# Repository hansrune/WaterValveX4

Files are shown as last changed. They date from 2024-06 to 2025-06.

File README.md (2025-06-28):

# Valve Controller X4

Work in progress / still a prototype...

A DYI 4x valve controller based on ESP32c3. This device is mainly intended for irrigation control, typically using 12V solenoid valves. You can also use ball valves with automatic return on power off.

This board is tested with ESPhome and ESPEasy [firmware](#firmwares) (build instructions below), and is easily used with home automation systems that support MQTT auto discovery, the native Home Assistant API, and the many [controllers that ESPEasy supports](https://espeasy.readthedocs.io/en/latest/Controller/_Controller.html)

## Introduction

Some of the main features and benefits

- **4x outputs**
    - For controlling up to four valves at a time
    - Each valve should draw less than 1A - or you can add to the PCB trace thickness using wire
- **Flow sensor input**
    - A flow sensor input is available
    - Can be open collector / hall sensor. Pulled up to 3.3V level internally. 5V supply on terminal
- **I2C support**
    - An I2C pin header with power supply is available to use with I2C sensors
    - ... or you can use the same GPIO pins for any other purpose of your choise
- **WiFi based**
    - This is almost a must have for most home automation systems
    - OTA support
    - Configuration backup, restore and bulk updates.
- **Firmware of your choise**
    - ESPEasy with Domoticz over http. Device creation uses virtual sensors
    - ESPEasy with Domotics and Home Assistant via MQTT. Device creation uses a MQTT configuration text file.
    - ESPHome to Home Assistant via MQTT and auto discovery
    - ESPHome to Domoticz via MQTT and auto discovery
    - ... and as the hardware supports using both Arduino and ESP-IF development kits, almost any other firmware can be created.
- **Seed Studio XIAO ESP32C3**
    - This device is shielded and comes with an external IPX antenna connector
    - FCC and CE regulations approved

## Setup and mounting

The main parts includes a simple flow sensor and a pressure reduction device:

<p align="center">
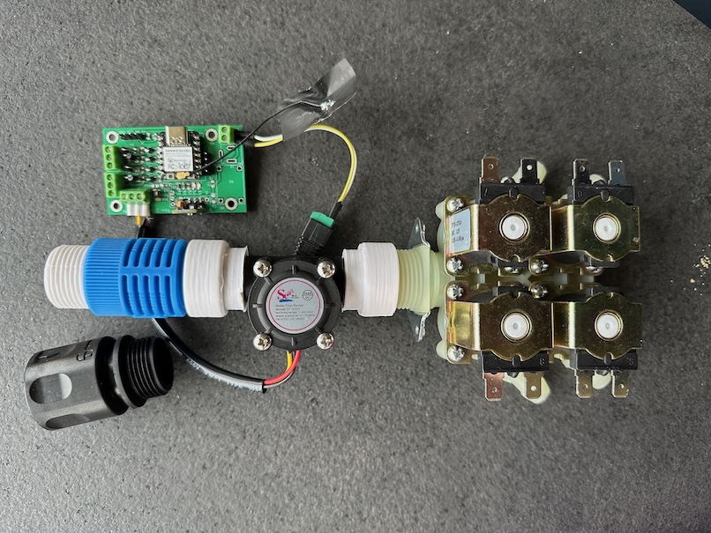
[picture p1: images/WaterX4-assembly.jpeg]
    
</p>

The adapter parts are [3D prints](./FreeCAD/README.md)

I use a long box with a closing / latched lid. This is designed for outdoor use. Will tolerate rain, but not frost.

<p align="center">
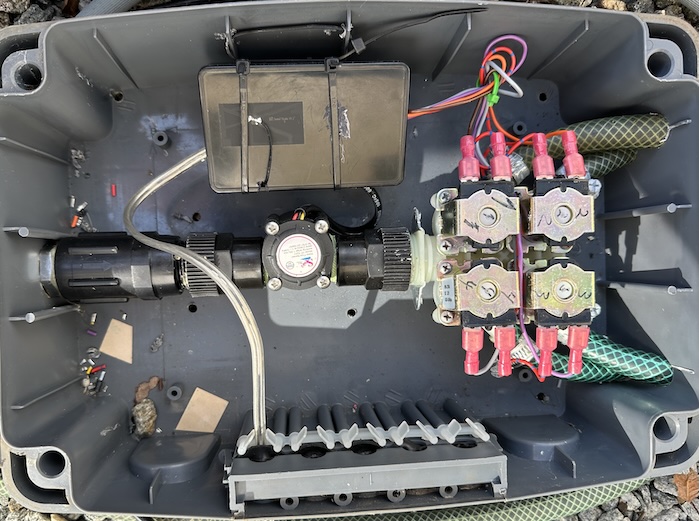
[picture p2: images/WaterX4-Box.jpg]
    
</p>

Please note the bottom holes. In case water is leaked, it has a way to drain out of the box

## Indicators

Each of the four valve outputs has a LED indicator at the back of the PCB

- LED D11 will indicate low level input from the flow meter
- LED D1
  - no change indicates out of power, device death/freeze or other
  - a duty cycle 1:1 will indicate a reset is ongoing
<!--
  - will blink with a duty cycle 1-4 or 4-1 to indicate valve closed or open
-->

## Implementation and design

The schematic diagram is [available here](KiCad/WaterValveX4-schema-2.0.1.pdf). The [KiCad EDA](https://www.kicad.org/) project is in the [same folder](./KiCad)

### GPIO pin usage

| PIN | Capabilty | Function |
|---|---|---|
| GPIO2 | Acticve low output | LED D2 - not used |
| GPIO3 | Active high output | Valve 1 |
| GPIO4 | Active high output | Valve 2 |
| GPIO5 | Active high output | Valve 3 |
| GPIO6 | I2C | SDA |
| GPIO7 | I2C | SCL |
| GPIO8 | Active high output | Valve 4 |
| GPIO9 | Active low out | Status LED |
| GPIO10 | Pulled up input | Flow meter input |
| GPIO20 | RX / 1-wire | Serial or 1-wire sensor |
| GPIO21 | TX / 1-wire | Serial or 1-wire sensor |

## Hardware - getting started

This project uses my [KiCad-lib-ESP32 repository](https://github.com/hansrune/KiCad-lib-ESP32.git) as a [git submodule](https://www.git-scm.com/book/en/v2/Git-Tools-Submodules). To check this out, use the following:

```bash
git clone --recurse-submodules https://github.com/hansrune/WaterValveX4.git 
```

### Materials used

This project uses the [Seed Studio XIAO ESP32C3 RISC-V module](https://www.seeedstudio.com/Seeed-XIAO-ESP32C3-p-5431.html). This tiny device has proven to be more reliable than most ESP8266 modules used in earlier versions. This module also comes with an IPX connector for connecting an external antenna, and is delivered with a simple external antenna for good range. This device is also EMI shielded and certified.

<!--
A ball valve like [these HSH-FLO valves](https://www.ebay.com/itm/121728665101?var=420727385309) uses metal gears, and also have a manual override possibility. Despite the moderate cost, I have found them very reliable. Manufacturer claims 100k operations. I typically use a 2 or some times 3-port version, size 3/4" DN20, DC12/24V and with CR05-01 wiring, including a manual overrride whell option.
-->
A 4x valve like the below attached with a washing machine attachment hose

<p align="center">
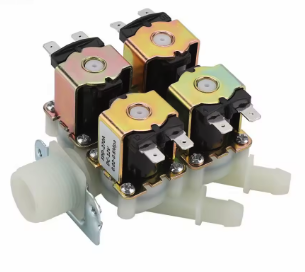
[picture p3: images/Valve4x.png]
    
</p>

A selection of 3D printable (STL and FreeCAD) adapters is available [here](./FreeCAD/README.md)

Any available 12V DC power supply delivering 2A or more should do for the control board and the valves.

There are many options and possible pinouts for DC-DC converters for the 12V to 5V conversion. A linear regulator (L7805) will need a heatsink, so a DC-DC converter is recommended.

<p align="center">
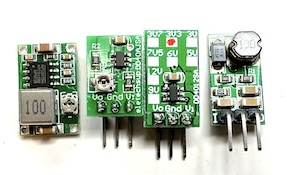
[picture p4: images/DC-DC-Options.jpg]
    
</p>

The MOSFETs need a low Vgs trigger voltage, i.e. well under 3V on full load. I have used Si2302/N025P for the N-channel, SOT-23 package.

Resistors are 0805 size. Screw terminals are 3.5mm, which is a tight fit when ferrules are being used.

For more information, use [this KiCad BOM](KiCad/WaterValveX4-BOM.csv)

## Hardware assembly

Soldering a prototype by hand is possible if you have a steady hand and a small solder iron tip. A microscope is recommended to inspect the solder joints properly.

Recommend to do the SMD parts first, then other components. 

### Hardware tests

You should test at least the following **before adding the ESP32 module**:

- Attach a battery and check that the valve can be operated both NO and NC
- Add power and check that 5V conversion is OK
- Apply 5V to GPIO 1, 5, 3 and 8 in turn to check that the output works with the indicators at the PCB back side

## Firmwares

### ESPHome

ESPHome firmware can be set up from [this ESPHome configuration repository](https://github.com/hansrune/esphome-config) using the `test_waterx4.yaml` file as a template

Follow the [README](https://github.com/hansrune/esphome-config) for instructions on what you will likely want to change.

By default, MQTT auto discovery is being used. This should work out of the box with Home Assistant, Domoticz and other that support [Home Assistant MQTT Auto Discovery](https://www.home-assistant.io/integrations/mqtt/#mqtt-discovery)

In Home Assistant, the device has these controls. Valves are labelled a, b, c and d. The -1 is the controller instance

<p align="center">
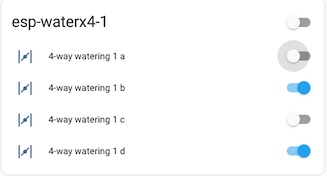
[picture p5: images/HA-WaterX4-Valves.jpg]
    
</p>

... and flow sensor / total counter:

<p align="center">
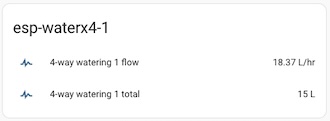
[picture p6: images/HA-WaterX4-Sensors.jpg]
    
</p>

### ESPEasy

ESPEasy can be used with a number of different controllers / home automation systms. A custom firmware build description is [available here](https://github.com/hansrune/ESPEasy-custom/blob/builds/custom/mega-20240822-1/README-custombuilds.md)

ESPEasy requires many settings. For configuration settings and rule files, you can upload the files from [this page](./ESPEasy/) as a starting point. Please make sure to change name, unit number, controller IP addresses, NTP, syslog host and latitude/longitude. This configuration uses both a MQTT controller and a Domoticz controller. Change to what you need.

## Bugs and tweaks

Version 2.0 of the PCB needs the flow sensor input components mounted as shown:

<p align="center">
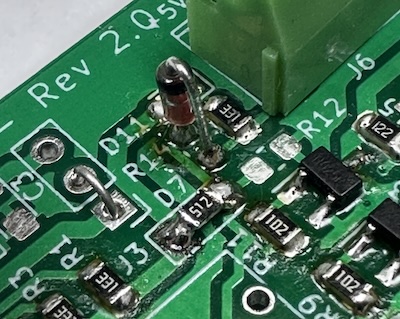
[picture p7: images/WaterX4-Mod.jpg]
    
</p>

- A 1N4148 diode replaces R14 - cathode faces terminal connector
- A 5.1 kohm resistor replaces D7 - for a pull-up
- R12 is not mounted

<!-- 

## How to contribute

-->

## Licensing

This project is licensed under the [GNU General Public License v3.0](GNU-LICENSE-V3.txt) for the software, [CERN-OHL-W](OHL-LICENSE.txt) for the hardware, and [CC BY-SA](CC-BY-SA-LICENCE.txt) for the documentation and ideas.

<p align="center" width="100%">
    
</p>

<!-- 
| **Open Source Licenses** | |
| ---|---|
| Hardware | [CERN-OHL-W](OHL-LICENSE.txt) |
| Software | [GNU General Public License v3.0](GNU-LICENSE-V3.txt) |
| Documentation / idea | [CC BY-SA](CC-BY-SA-LICENCE.txt) |
-->

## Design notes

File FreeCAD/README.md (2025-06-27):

## Adapters

Below is a selection of 3D printed adapters I have used. These are all BSP threads.

Printed with ABS filament and a 0.8mm nozzle for durability

- 1/2" female to 1/2" female

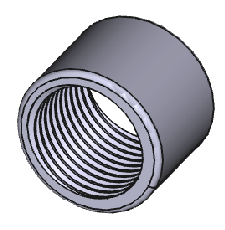
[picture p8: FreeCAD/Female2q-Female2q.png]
    

- 1/2" female to 3/4" female

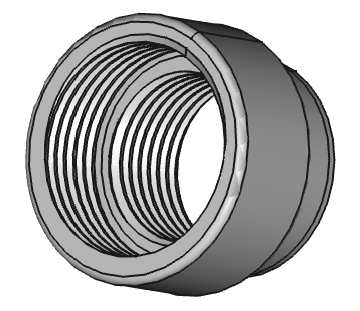
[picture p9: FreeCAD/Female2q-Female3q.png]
    

- 1/2" female to 3/4" male

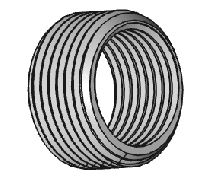
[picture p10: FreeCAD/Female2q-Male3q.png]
    

- 1/2" male to 1/2" male

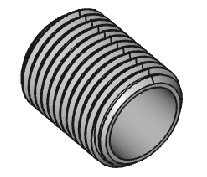
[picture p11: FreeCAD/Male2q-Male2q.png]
    

- 3/4" male to 3/4" male

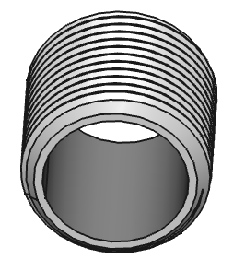
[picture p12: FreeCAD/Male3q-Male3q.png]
    

- 3/4" female to 3/4" female

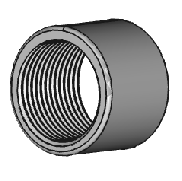
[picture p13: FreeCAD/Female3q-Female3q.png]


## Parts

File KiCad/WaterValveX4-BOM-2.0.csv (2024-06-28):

Id | Designator | Footprint | Quantity | Designation | Supplier and ref
1 | C3,C1 | CP_EIA-3216-18_Kemet-A_Pad1.58x1.35mm_HandSolder | 2 | 10uF
2 | J1,J5 | PinHeader_1x04_P2.54mm_Vertical | 2 | Conn_01x04_Male
3 | J2 | BarrelJack1 | 1 | Barrel_Jack
4 | J3 | PinHeader_1x03_P2.54mm_Vertical | 1 | Conn_01x03_Male
5 | Q1,Q2,Q3,Q4 | SOT-23_Handsoldering | 4 | IRLB3034
6 | R8,R6,R11,R9 | R_0805_2012Metric_Pad1.20x1.40mm_HandSolder | 4 | 1k
7 | R5,R4,R2 | R_0805_2012Metric_Pad1.20x1.40mm_HandSolder | 3 | 10k
8 | R7,R10,R3,R13,R15,R1,R16 | R_0805_2012Metric_Pad1.20x1.40mm_HandSolder | 7 | 330
9 | U2 | XIAO_ESP32C3_THT | 1 | SeedStudio XIAO ESP32 C3 v1
10 | U3 | TO-220-3_Vertical | 1 | L7805
11 | C2 | C_0805_2012Metric_Pad1.18x1.45mm_HandSolder | 1 | 100nF
12 | D2,D1,D11,D3,D8,D10,D5 | LED_0805_2012Metric_Pad1.15x1.40mm_HandSolder | 7 | LED
13 | J7,J8,J6 | TerminalBlock_Phoenix_PT-1,5-3-3.5-H_1x03_P3.50mm_Horizontal | 3 | Screw_Terminal_01x03
14 | U1 | DCDC_01 | 1 | Project_DCDC_01
15 | D4,D6,D9,D12 | D_DO-41_SOD81_P3.81mm_Vertical_KathodeUp | 4 | 1N4007
16 | J4 | PinHeader_1x01_P2.54mm_Vertical | 1 | Conn_01x01_Male
17 | H7,H5,H8,H6 | MountingHole_3.2mm_M3_ISO14580_Pad | 4 | MountingHole_Pad
18 | D7 | D_MiniMELF | 1 | 1N4148
19 | J9 | TerminalBlock_Phoenix_PT-1,5-2-3.5-H_1x02_P3.50mm_Horizontal | 1 | Screw_Terminal_01x02
20 | R14 | R_0805_2012Metric_Pad1.20x1.40mm_HandSolder | 1 | 2.2k
21 | R12 | R_0805_2012Metric_Pad1.20x1.40mm_HandSolder | 1 | 3.3k

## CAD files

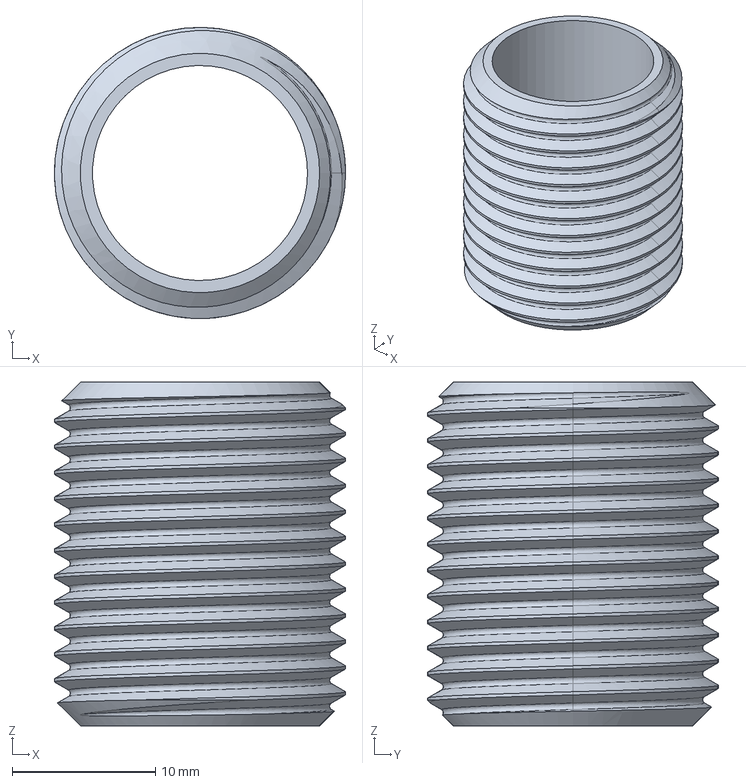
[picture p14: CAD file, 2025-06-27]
FreeCAD/Male2q-Male2q.FCStd
20.3 x 20.3 x 24.0 mm

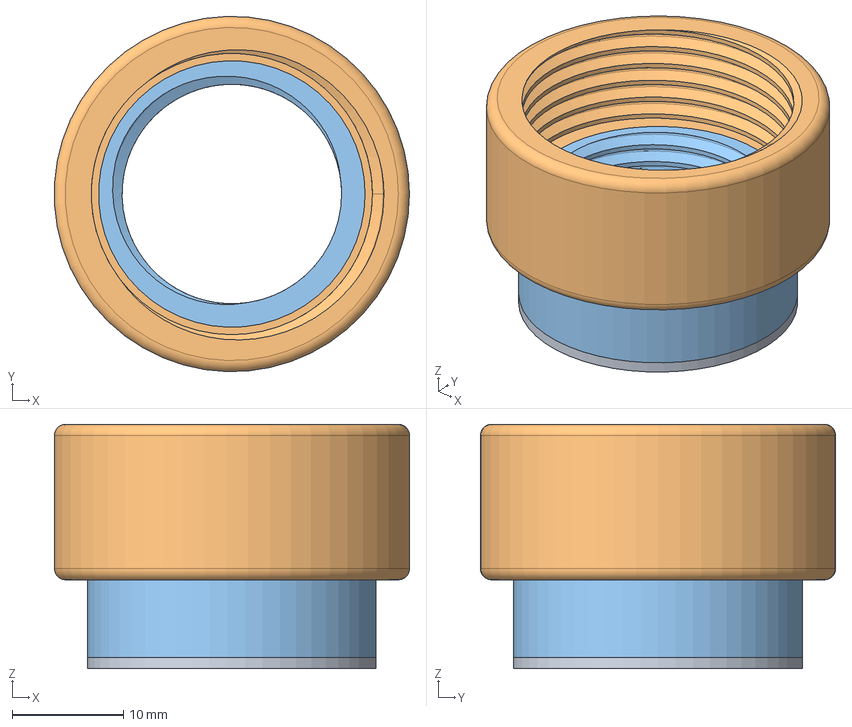
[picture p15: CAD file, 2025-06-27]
FreeCAD/Female2q-Female3q.FCStd
32.0 x 32.0 x 22.0 mm

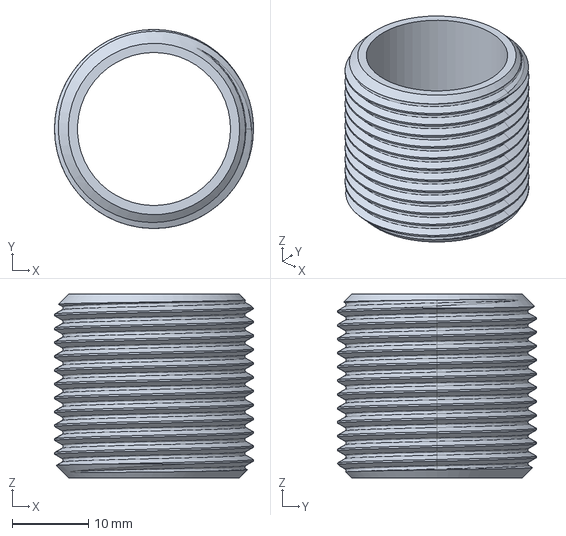
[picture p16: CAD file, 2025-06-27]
FreeCAD/Male3q-Male3q.FCStd
26.0 x 26.0 x 24.0 mm

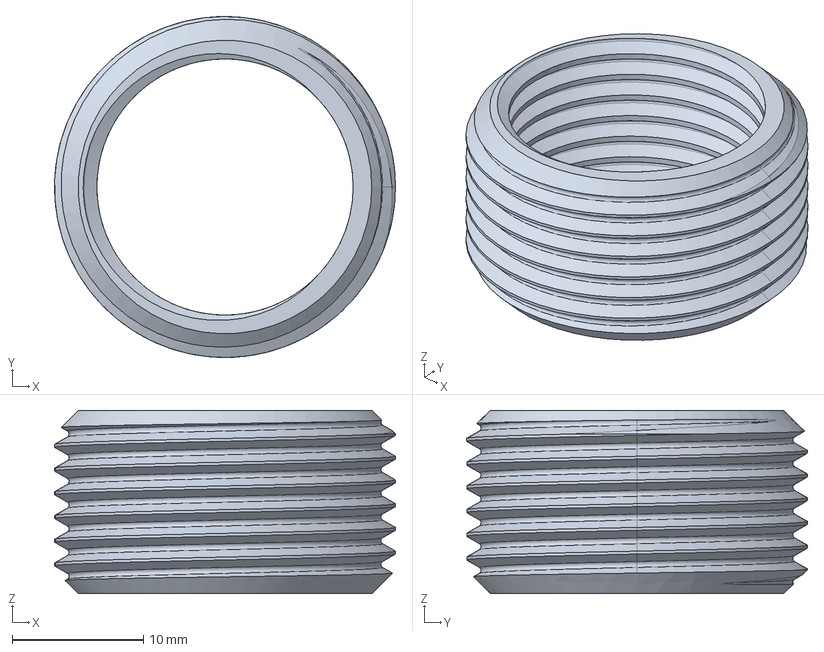
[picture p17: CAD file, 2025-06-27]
FreeCAD/Female2q-Male3q.FCStd
26.0 x 26.0 x 14.0 mm

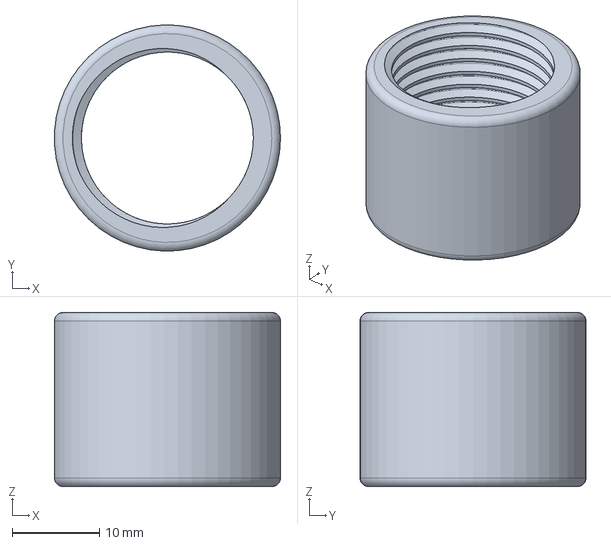
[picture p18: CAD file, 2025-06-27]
FreeCAD/Female2q-Female2q.FCStd
26.0 x 26.0 x 20.0 mm

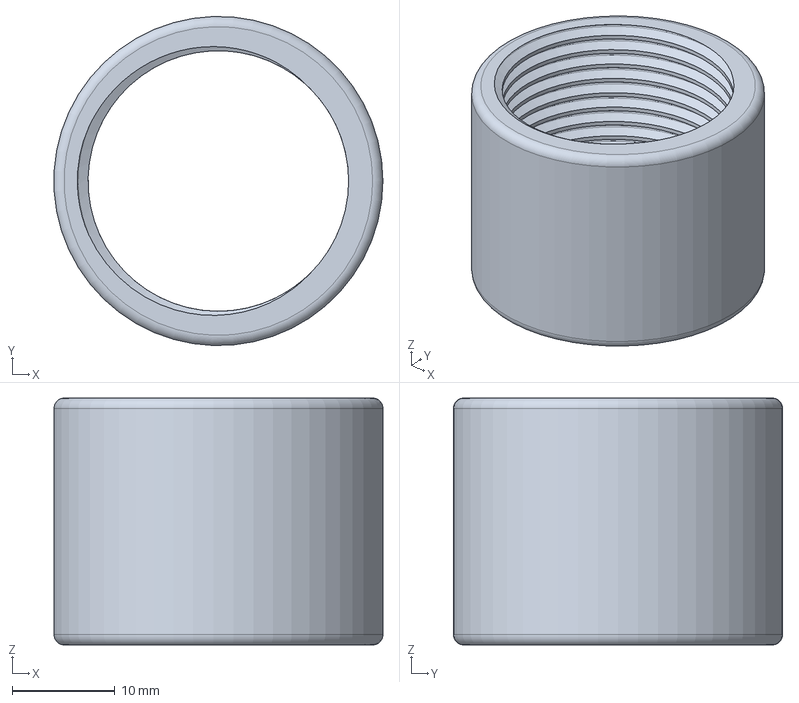
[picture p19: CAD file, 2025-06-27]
FreeCAD/Female3q-Female3q.FCStd
32.0 x 32.0 x 24.0 mm

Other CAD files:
FreeCAD/Male2q-Male2q.stl

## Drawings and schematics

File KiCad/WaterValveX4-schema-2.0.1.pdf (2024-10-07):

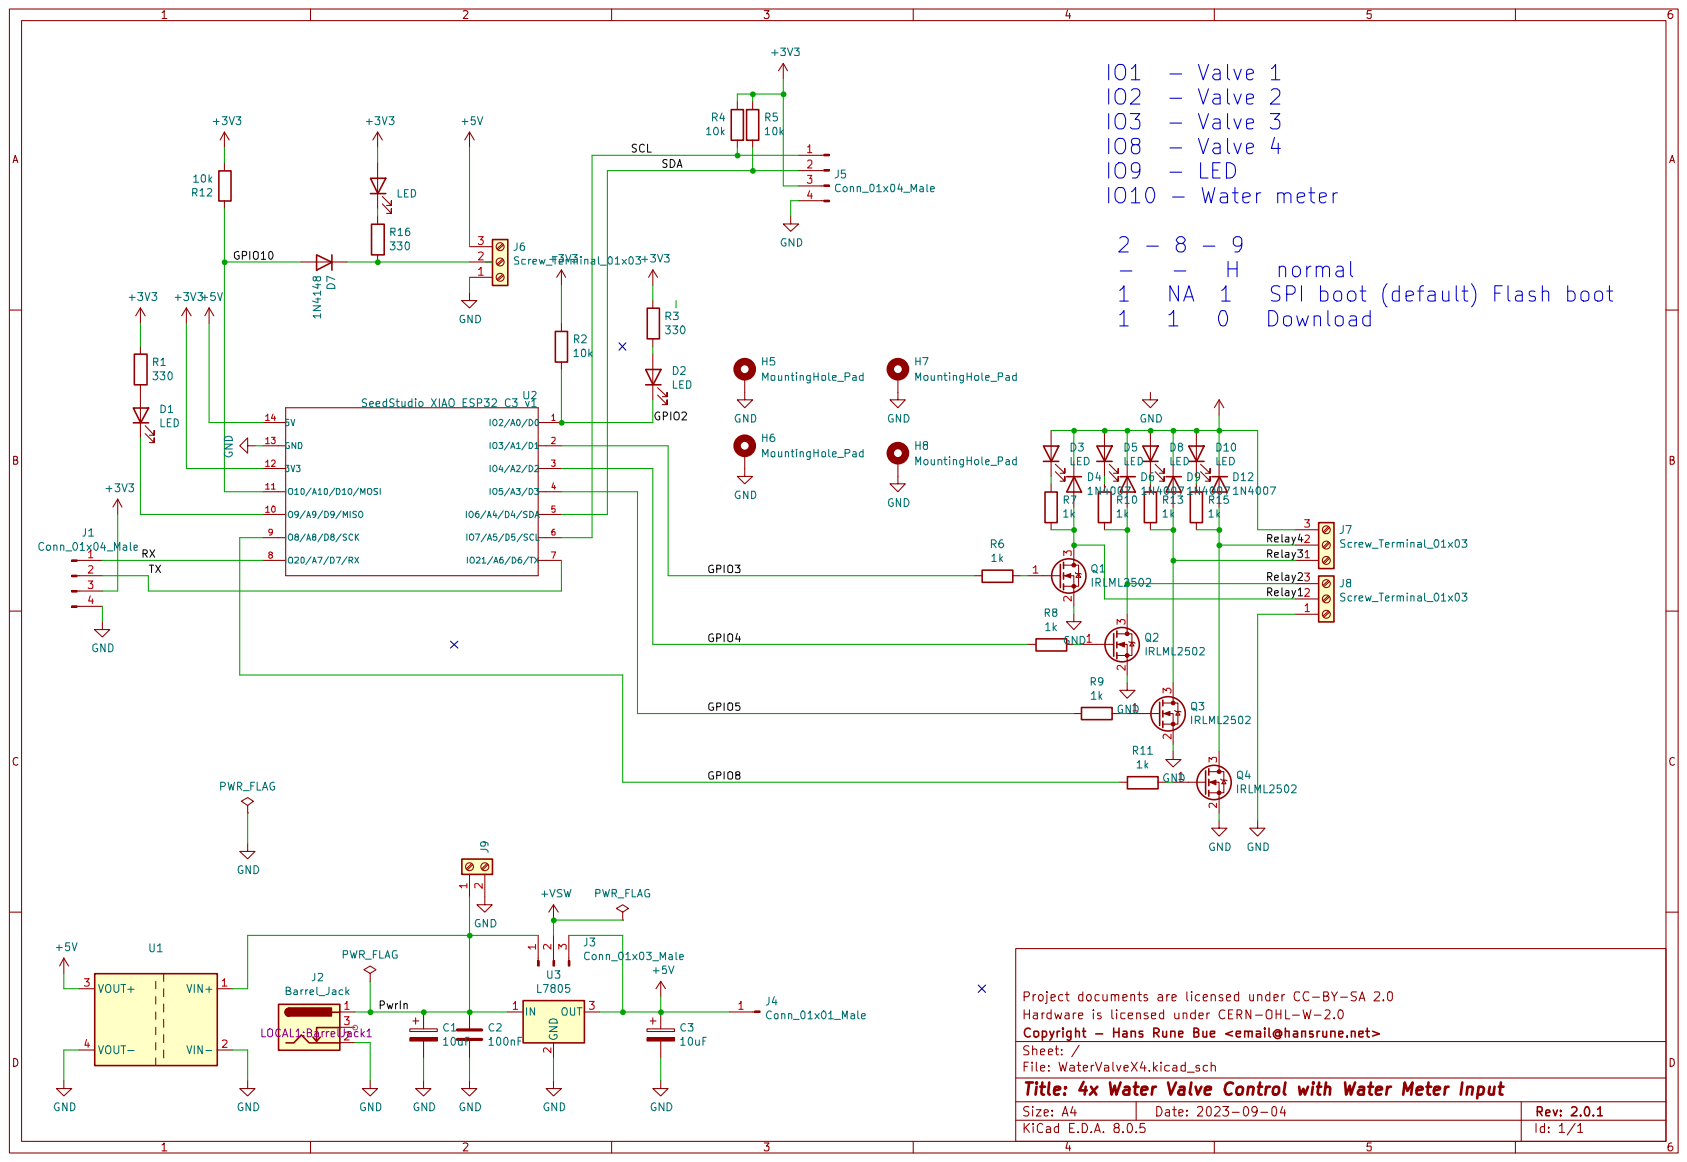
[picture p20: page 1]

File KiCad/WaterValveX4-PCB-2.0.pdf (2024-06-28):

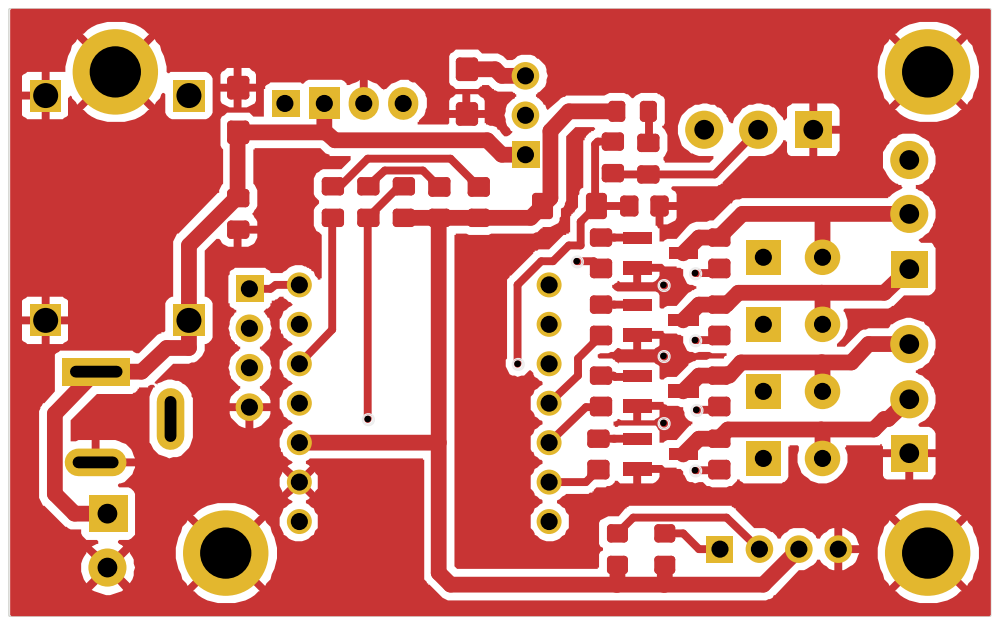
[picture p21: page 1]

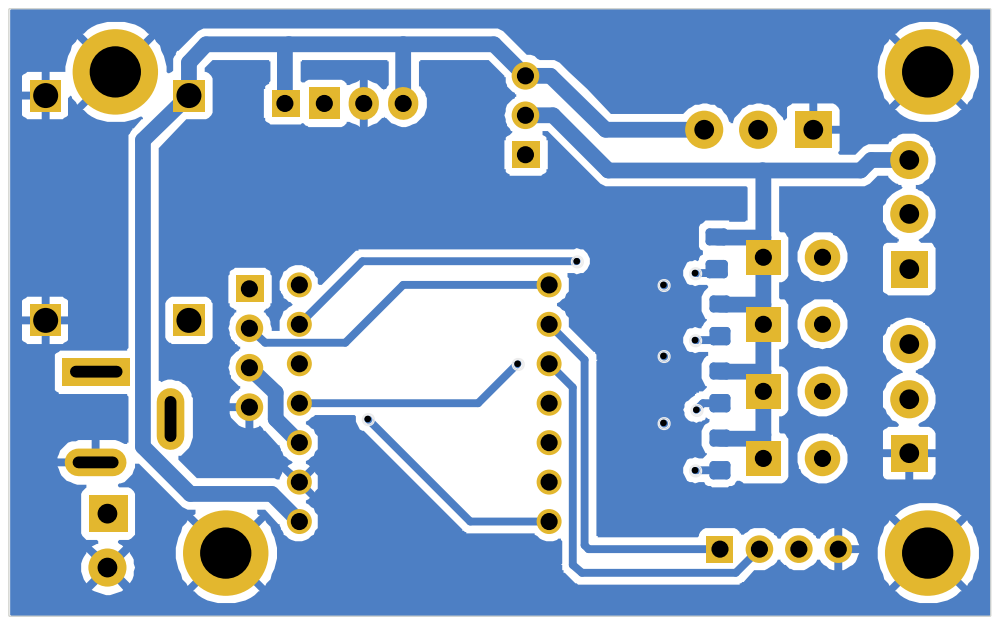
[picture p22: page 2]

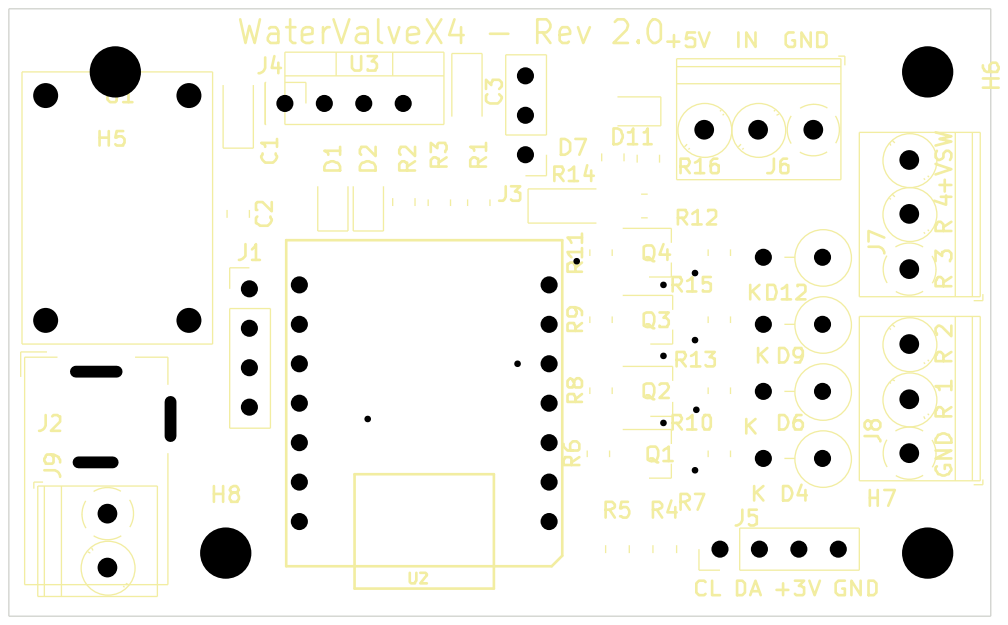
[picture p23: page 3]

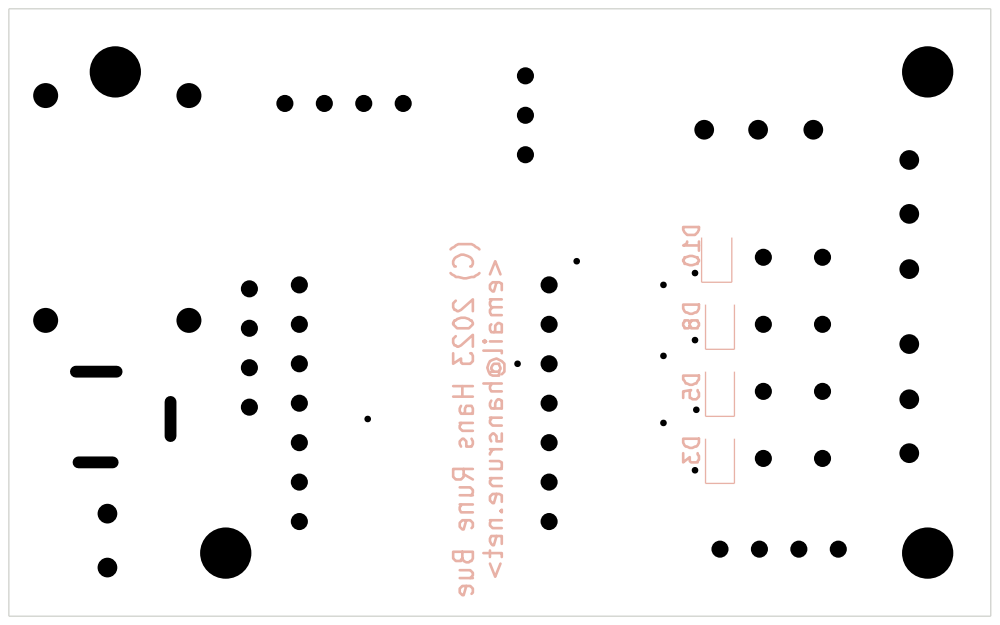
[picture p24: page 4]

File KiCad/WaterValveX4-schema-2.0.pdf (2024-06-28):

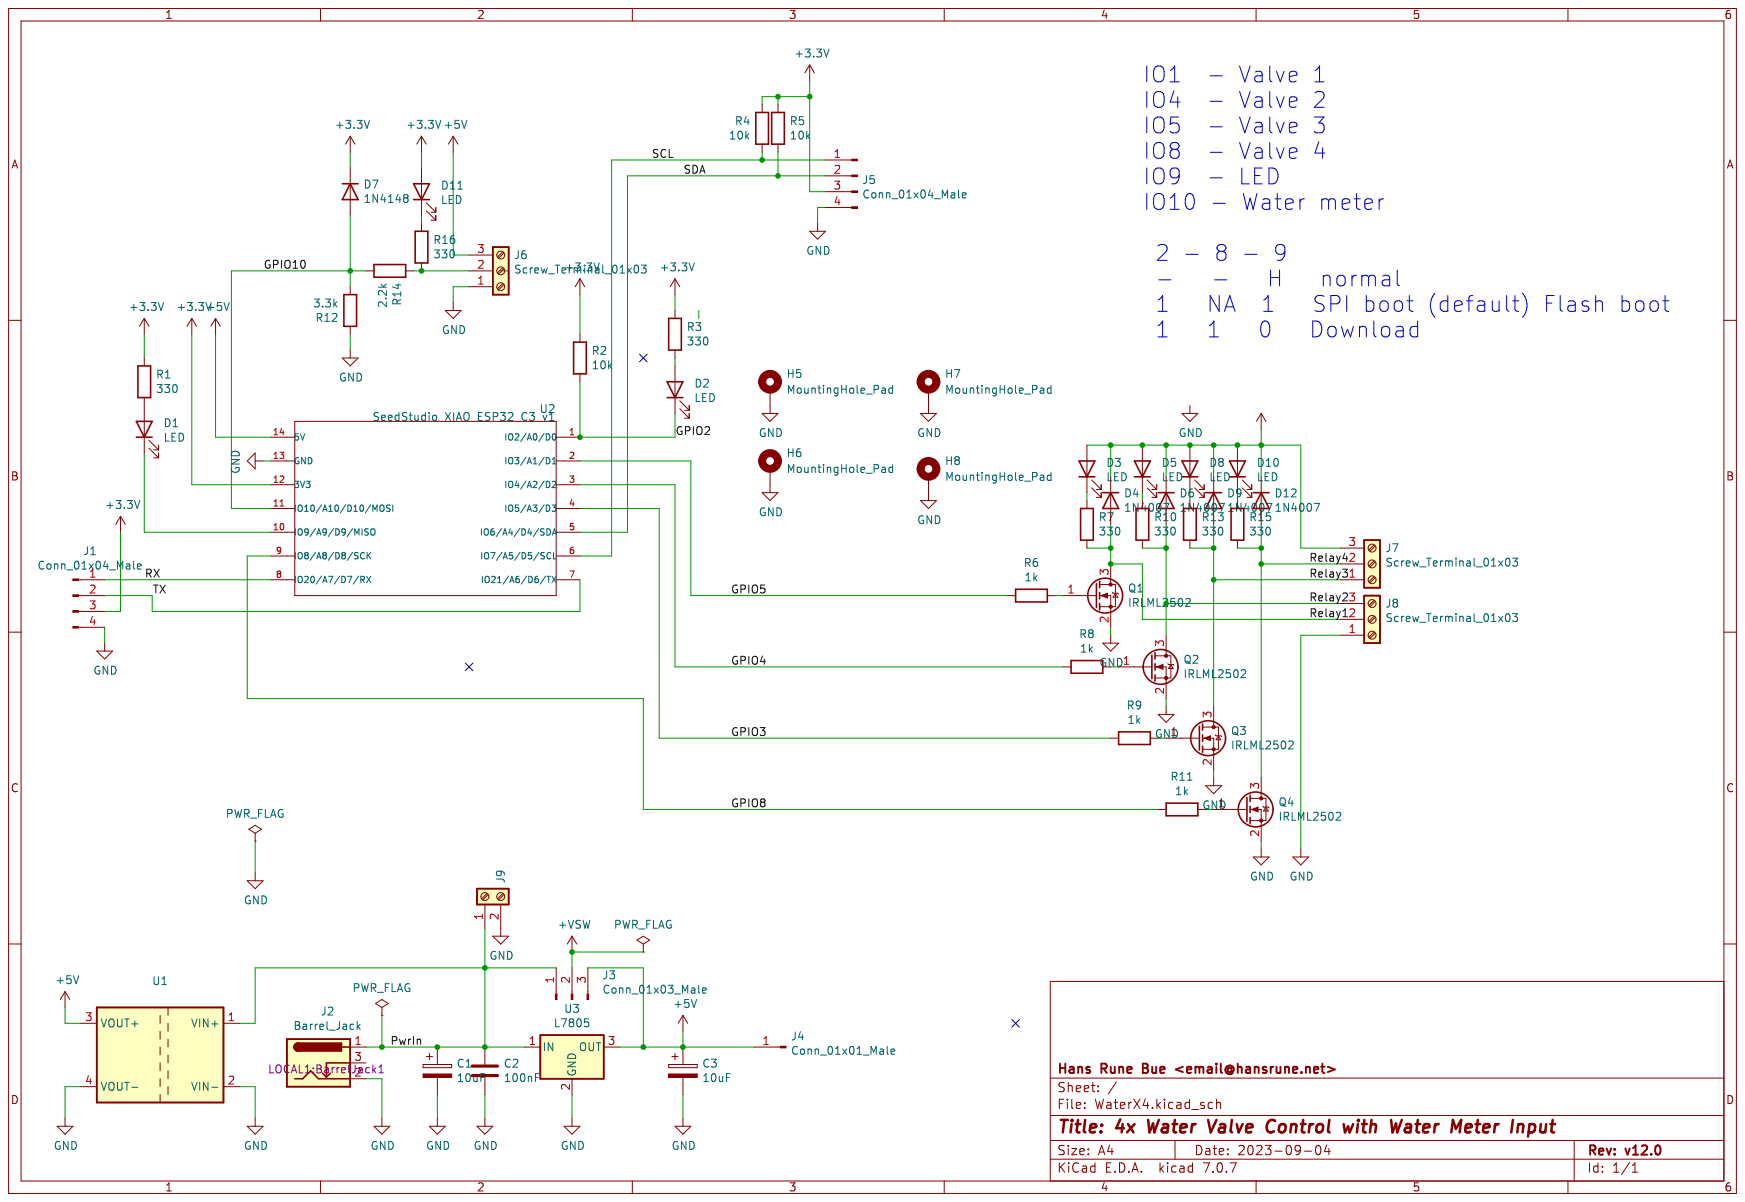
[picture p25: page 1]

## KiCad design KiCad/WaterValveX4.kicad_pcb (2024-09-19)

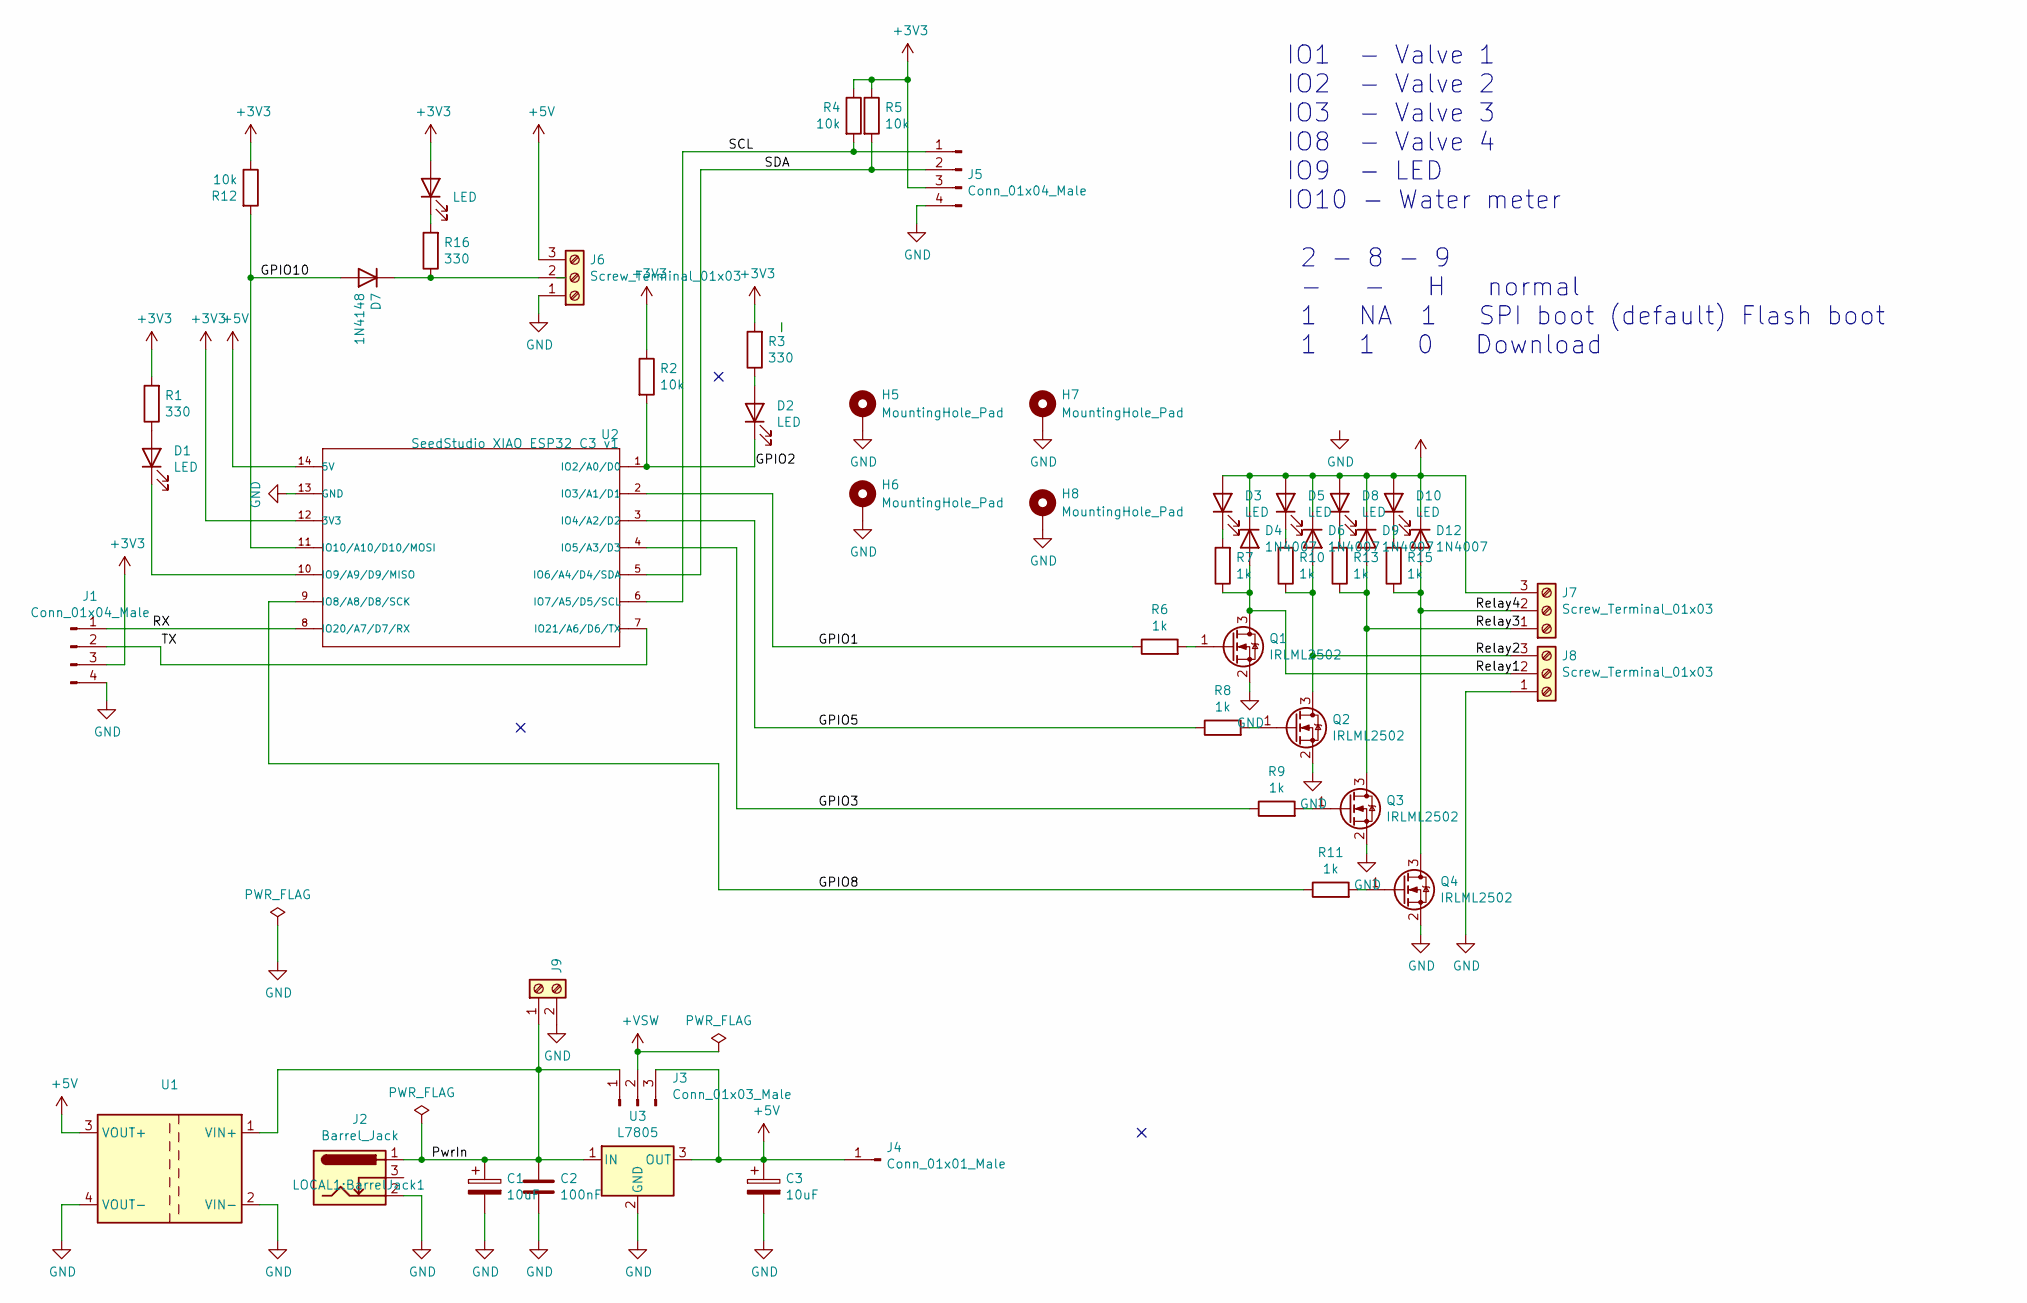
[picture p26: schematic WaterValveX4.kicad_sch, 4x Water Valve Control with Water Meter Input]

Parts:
C1, C3: 10uF; CP_EIA-3216-18_Kemet-A_Pad1.58x1.35mm_HandSolder
C2: 100nF; C_0805_2012Metric_Pad1.18x1.45mm_HandSolder
D1, D2, D3, D5, D8, D10, D11: LED; LED_0805_2012Metric_Pad1.15x1.40mm_HandSolder
D4, D6, D9, D12: 1N4007; D_DO-41_SOD81_P3.81mm_Vertical_KathodeUp
D7: 1N4148; D_MiniMELF
H5, H6, H7, H8: MountingHole_Pad; MountingHole_3.2mm_M3_ISO14580_Pad
J1, J5: Conn_01x04_Male; PinHeader_1x04_P2.54mm_Vertical
J2: Barrel_Jack; BarrelJack1
J3: Conn_01x03_Male; PinHeader_1x03_P2.54mm_Vertical
J4: Conn_01x01_Male; PinHeader_1x01_P2.54mm_Vertical
J6, J7, J8: Screw_Terminal_01x03; TerminalBlock_Phoenix_PT-1,5-3-3.5-H_1x03_P3.50mm_Horizontal
J9: Screw_Terminal_01x02; TerminalBlock_Phoenix_PT-1,5-2-3.5-H_1x02_P3.50mm_Horizontal
Q1, Q2, Q3, Q4: IRLML2502; SOT-23_Handsoldering
R1, R3, R16: 330; R_0805_2012Metric_Pad1.20x1.40mm_HandSolder
R2, R4, R5, R12: 10k; R_0805_2012Metric_Pad1.20x1.40mm_HandSolder
R6, R7, R8, R9, R10, R11, R13, R15: 1k; R_0805_2012Metric_Pad1.20x1.40mm_HandSolder
U1: Project_DCDC_01; DCDC_01
U2: SeedStudio XIAO ESP32 C3 v1; XIAO_ESP32C3_THT
U3: L7805; TO-220-3_Vertical

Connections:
+3V3: D11.2 (A), J1.3, J5.3, R1.2, R2.1, R3.2, R4.1, R5.1, R12.1, U2.12 (3V3)
+5V: C3.1, J3.3, J4.1, J6.3, U1.3 (VOUT+), U2.14 (5V), U3.3 (OUT)
+VSW: D3.2 (A), D4.1 (K), D5.2 (A), D6.1 (K), D8.2 (A), D9.1 (K), D10.2 (A), D12.1 (K), J3.2, J7.3
/GPIO1: R6.1, U2.2 (IO3/A1/D1)
/GPIO2: D2.1 (K), R2.2, U2.1 (IO2/A0/D0)
/GPIO3: R9.1, U2.4 (IO5/A3/D3)
/GPIO5: R8.1, U2.3 (IO4/A2/D2)
/GPIO8: R11.1, U2.9 (IO8/A8/D8/SCK)
/GPIO10: D7.2 (A), R12.2, U2.11 (IO10/A10/D10/MOSI)
/PwrIn: C1.1, C2.1, J2.1, J3.1, J9.1, U1.1 (VIN+), U3.1 (IN)
/RX: J1.1, U2.8 (IO20/A7/D7/RX)
/Relay1: D4.2 (A), J8.2, Q1.3 (D), R7.1
/Relay2: D6.2 (A), J8.3, Q2.3 (D), R10.1
/Relay3: D9.2 (A), J7.1, Q3.3 (D), R13.1
/Relay4: D12.2 (A), J7.2, Q4.3 (D), R15.1
/SCL: J5.1, R4.2, U2.6 (IO7/A5/D5/SCL)
/SDA: J5.2, R5.2, U2.5 (IO6/A4/D4/SDA)
/TX: J1.2, U2.7 (IO21/A6/D6/TX)
GND: C1.2, C2.2, C3.2, H5.1, H6.1, H7.1, H8.1, J1.4, J2.2, J5.4, J6.1, J8.1, J9.2, Q1.2 (S), Q2.2 (S), Q3.2 (S), Q4.2 (S), U1.2 (VIN-), U1.4 (VOUT-), U2.13 (GND), U3.2 (GND)
unnamed: D1.2 (A), R1.1
unnamed: D1.1 (K), U2.10 (IO9/A9/D9/MISO)
unnamed: D2.2 (A), R3.1
unnamed: D3.1 (K), R7.2
unnamed: D5.1 (K), R10.2
unnamed: D7.1 (K), J6.2, R16.1
unnamed: D8.1 (K), R13.2
unnamed: D10.1 (K), R15.2
unnamed: D11.1 (K), R16.2
unnamed: Q1.1 (G), R6.2
unnamed: Q2.1 (G), R8.2
unnamed: Q3.1 (G), R9.2
unnamed: Q4.1 (G), R11.2

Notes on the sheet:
IO1 - Valve 1 IO2 - Valve 2 IO3 - Valve 3 IO8 - Valve 4 IO9 - LED IO10 - Water meter 2 - 8 - 9 - - H normal 1 NA 1 SPI boot (default) Flash boot 1 1 0 Download

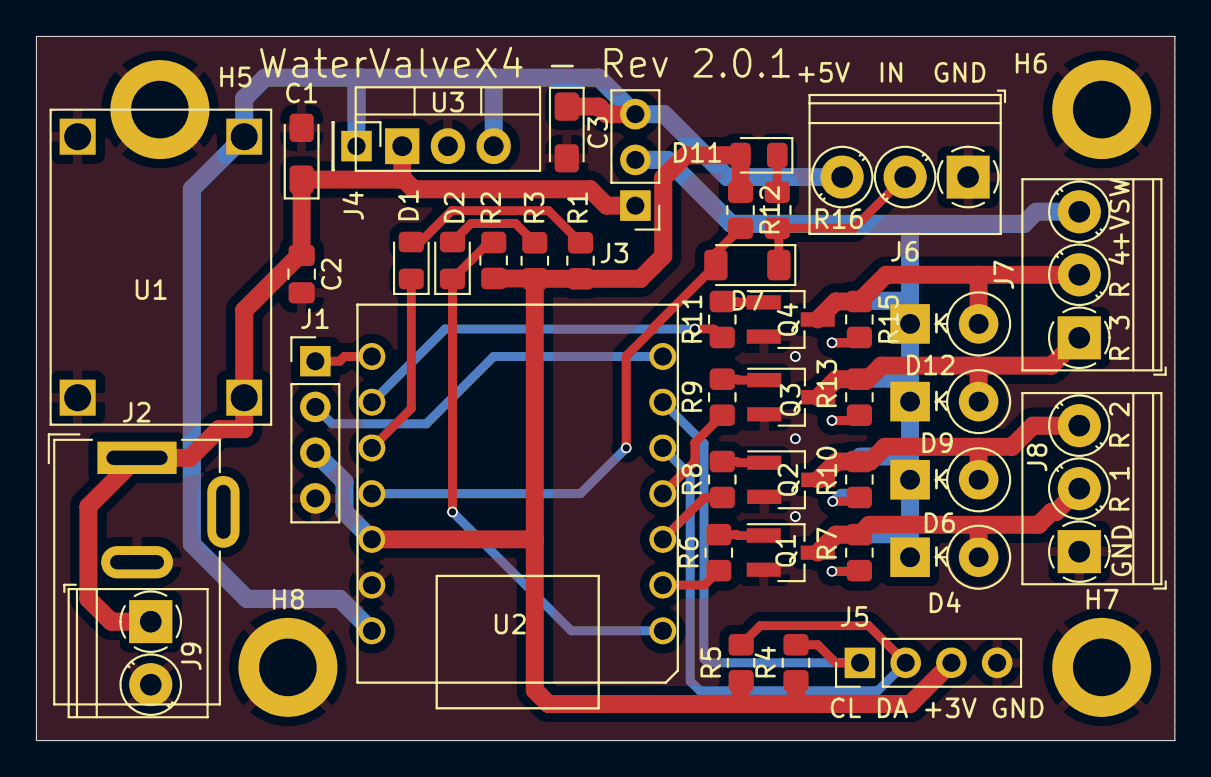
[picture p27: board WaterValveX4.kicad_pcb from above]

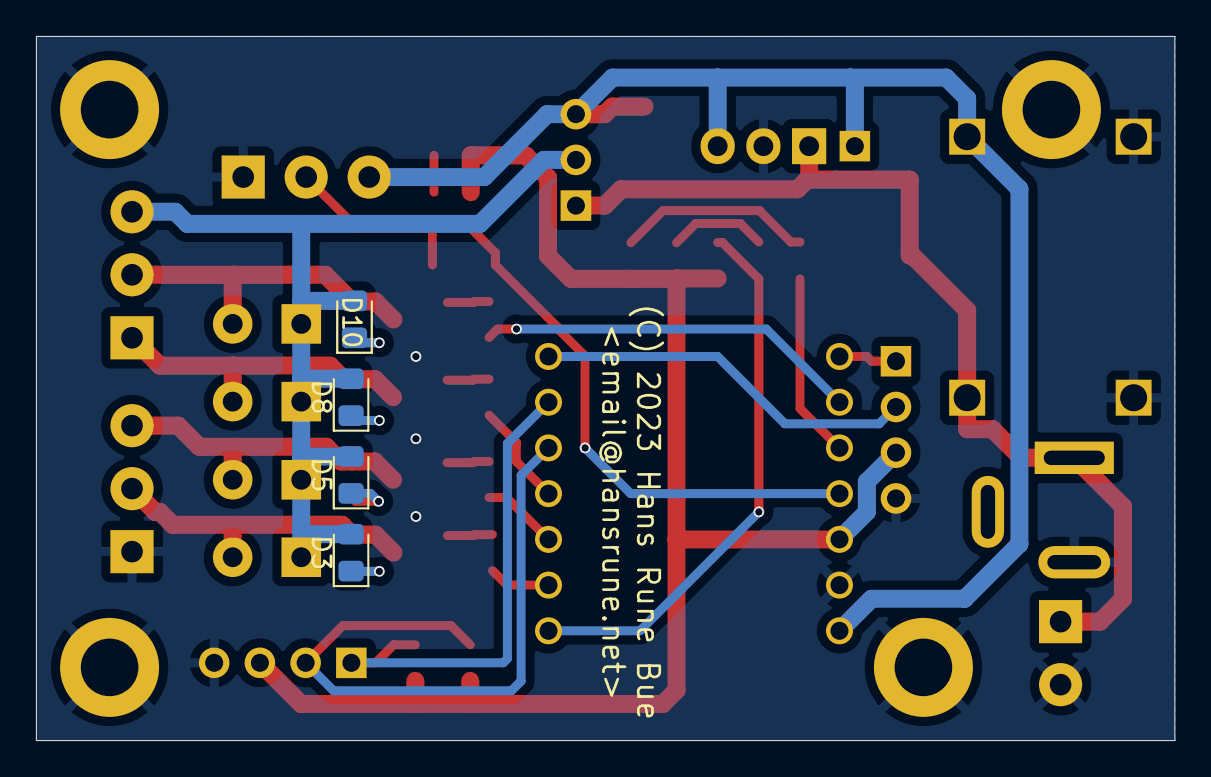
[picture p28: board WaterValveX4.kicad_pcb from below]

Board: 2 copper layers, 63.2 x 39.1 mm, 50 parts (4 on the bottom side), 32 nets.

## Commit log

2024-06-28 Version 2.0 - intial git version
    [WaterValveX4-BOM-2.0.csv, WaterValveX4.kicad_pcb, WaterValveX4.kicad_sch]
2024-06-28 Version 2.0.1 - pulled up / level shifted flow input
    [WaterValveX4.kicad_pcb, WaterValveX4.kicad_sch]
2024-06-30 Add version 2.0.1 schema PDF print
2024-09-19 New 3D model
    [WaterValveX4.kicad_pcb]
2024-10-07 Fixed KiCAD GPIO labels
    [WaterValveX4.kicad_sch]
2025-06-14 Update README.md - no ball valve used
2025-06-27 Added 3D parts
    [Female2q-Female2q.FCStd, Female2q-Female3q.FCStd, Female2q-Male3q.FCStd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]
2025-06-27 Added README for the 3D print adapters

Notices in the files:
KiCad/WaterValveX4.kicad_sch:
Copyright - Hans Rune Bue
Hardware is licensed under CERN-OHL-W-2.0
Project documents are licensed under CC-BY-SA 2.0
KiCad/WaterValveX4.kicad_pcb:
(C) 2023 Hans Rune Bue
